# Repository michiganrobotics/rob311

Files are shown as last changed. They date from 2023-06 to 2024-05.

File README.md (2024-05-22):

# Robotics 311: How to Build Robots and Make Them Move

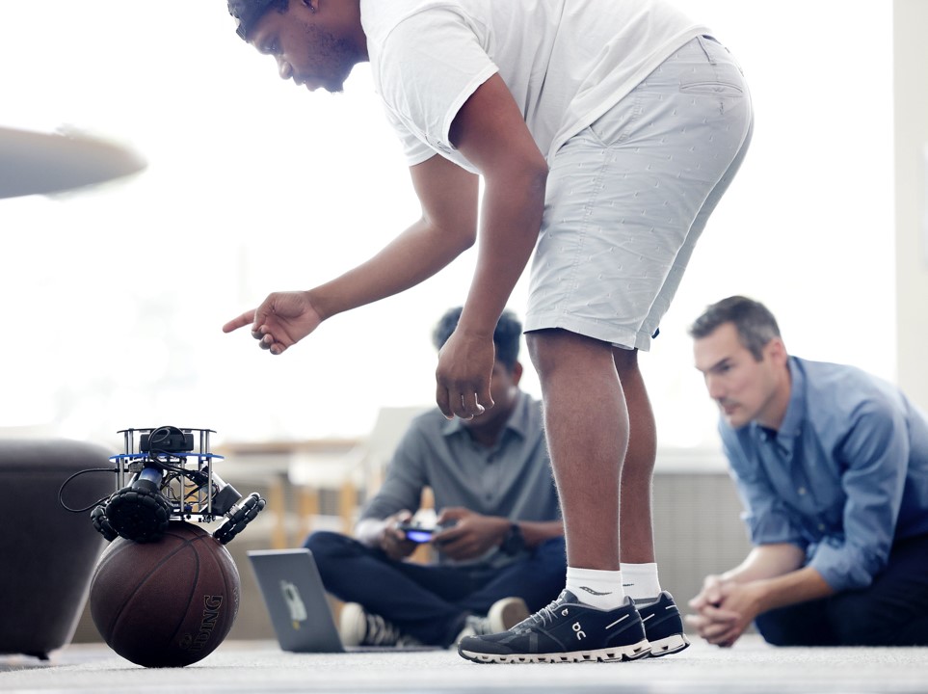
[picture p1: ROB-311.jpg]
Yves points at a ballbot


ROB 311 is an undergraduate robotics course at the University of Michigan that introduces the fundamentals of mechanical design, control, fabrication, actuation, instrumentation, and computer interfaces required to realize robotic systems. Students will learn to analyze/simulate rigid body kinematics, kinetics, and dynamics, as well as assess the impedance properties of their designs.

This first iteration was offered in Fall 2022. The course is based around building a ballbot, which balances on a basketball to move around.

## Lectures
All lecture videos are available on YouTube: [ROB 311 Fall 2022 Playlist](https://www.youtube.com/watch?v=aZ-mrETfKmE&list=PLdPQZLMHRjDIWDJDjiBKjFe7ETD_rssB9)

If a lecture features additional files, those are located in [lecture files](https://github.com/michiganrobotics/rob311/tree/main/Lecture%20Files).

## Labs and hardware

[Labs](https://github.com/michiganrobotics/rob311/tree/main/Labs) are based around the design and build of the ballbot, requiring certain hardware and access to machines, including 3D printer, laser cutter, and water jet.

The parts list (or [see full bill of materials](https://github.com/michiganrobotics/rob311/blob/main/Resources/Ballbot%20Bill%20of%20Materials.pdf)):
- Raspberry Pi Pico
- BlinkM led
- 3 Pololu 37D gearmotors
- 3 motor couplers
- acrylic sheets
- velcro strips
- 6 omni wheel halves
- 2 wired mouse
- basketball

Note lab 1, a primer on soldering, is not included in this repository, and lab 5 is skipped.

## Course Plan
| Lecture | Topic | YouTube | Assignments Due |
|---|---|---|---|
| 1 | Introduction to robot development | [Video](https://www.youtube.com/watch?v=aZ-mrETfKmE) | |
| L1 | Lab: Soldering | | |
| 2 | Motors, transmissions, & drivers I  | [Video](https://www.youtube.com/watch?v=Mq1Bgk68PBI) | |
| 3 | Motors, transmissions, & drivers II | [Video](https://www.youtube.com/watch?v=Oz2Eo8m5Dek) | |
| L2 | Lab: Raspberry Pi's | | |
| 4 | Mechanical modeling | [Video](https://www.youtube.com/watch?v=HCKUdEtMk7Y) | |
| 5 | Modeling & design | [Video](https://www.youtube.com/watch?v=dP0wdarfrkY) | HW 1 |
| L3 | Lab: Solidworks | | |
| 6 | Thermal modeling | [Video](https://www.youtube.com/watch?v=CyqpaNBj9x0) | |
| 7 | Manufacturing | [Video](https://www.youtube.com/watch?v=a9g4DT3PtMI) | |
| L4 | Lab: Lasercutting | | |
| 8 | Additive manufacturing | [Video](https://www.youtube.com/watch?v=YzE1I1oQzHI) | |
| 9 | Subtractive manufacturing | [Video](https://www.youtube.com/watch?v=Pls2lRZjnxo) | |
| L6 | Lab: Ballbot assembly | | Ballbot assembled |
| 10 | Manufacturing best practices | [Video](https://www.youtube.com/watch?v=BBs-HmwfgLc) | |
| 11 | Gears, screws & linkages | [Video](https://www.youtube.com/watch?v=xYcbeahHpbk) | |
| L7 | Lab: Python | | |
| 12 | Full planar model | [Video](https://www.youtube.com/watch?v=MVAvgaW5twc) | HW 2 |
| 13 | Torque conversion | [Video](https://www.youtube.com/watch?v=8ChdTWNvGpY) | |
| L8 | Lab: Closed loop control | | |
| 14 | Kinematic conversions | [Video](https://www.youtube.com/watch?v=uLpom1g87a0) | |
| L9 | Lab: Kinematics | | |
| 15 | Sensors | [Video](https://www.youtube.com/watch?v=9VtycgTxyyI) | HW 3 |
| 16 | Digital communications | [Video](https://www.youtube.com/watch?v=Y-86CC3WgMU) | |
| L10 | Lab: Stability control | | |
| 17 | Omni wheels | [Video](https://www.youtube.com/watch?v=Ykprm8sEqzw) | |
| 18 | Ballbot work session | No lecture | |
| L11 | Lab: Outer velocity loop control | | |
| 19 | Review | [Video](https://www.youtube.com/watch?v=hH9S14uijNM) | Midterm (not publicly available) |
| L12 | Lab: Virtual environments | | |
| 20 | Control | [Video](https://www.youtube.com/watch?v=tzFXzcDsMec) | HW 4 |
| 21 | Control loop structure | [Video](https://www.youtube.com/watch?v=KcQr0awXiuQ) | |
| L13 | Lab: Filtering data | | |
| 22 | Ballbot work session | No lecture | |
| 23 | Filtering data | [Video](https://www.youtube.com/watch?v=sBFdfnljp9M) | |
| L14 | Lab: Ballbot work session | | HW 5 |
| 24 | Steering control | [Video](https://www.youtube.com/watch?v=FliyuyiXhro) | |
| 25 | Final competition | | |

## Credits
- Elliott Rouse, Associate Professor, U-M
- Yves Nazon
- Senthur Ayyappan

## For more
- [University of Michigan Robotics](https://robotics.umich.edu)
- [Michigan Robotics Twitter](http://twitter.com/umrobotics)
- [Michigan Robotics Instagram](http://instagram.com/umrobotics/)
- [Michigan Robotics LinkedIn](https://www.linkedin.com/company/university-of-michigan-robotics/)

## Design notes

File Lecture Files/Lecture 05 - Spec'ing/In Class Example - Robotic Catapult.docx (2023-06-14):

In Class Example – Robotic Catapult

J_T : Total Inertia

J_m : Motor Inertia

J_(pm) : Point Mass Inertia= ml_a^2

τ_l : External Load=J_(pm) θ- mgl_a cos(θ)

ϕ_m : Motor Position=Nθ

Current Equation

k_t i=J_T ϕ_m +bϕ_m +(τ_l)/(ηN)

k_t i= (J_m +(ml_a^2)/(ηN^2))Nθ+bNθ+ (mgl_a cos(θ))/(ηN)

k_t i= J_m Nθ+(ml_a^2 θ)/(ηN)+bNθ+ (mgl_a cos(θ))/(ηN)

i=(J_m Nθ+(ml_a^2 θ)/(ηN)+bNθ+ (mgl_a cos(θ))/(ηN))/(k_t)

Voltage Equation

V=iR+L(di)/(dt)+k_t ϕ_m

V=iR+L(di)/(dt)+k_t Nθ

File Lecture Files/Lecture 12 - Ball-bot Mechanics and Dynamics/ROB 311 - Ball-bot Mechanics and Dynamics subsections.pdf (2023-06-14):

Planar System Modeling and Control

## 2 Planar System Modeling and Control

### 2.1 Model

### 2.1.1 Model Description

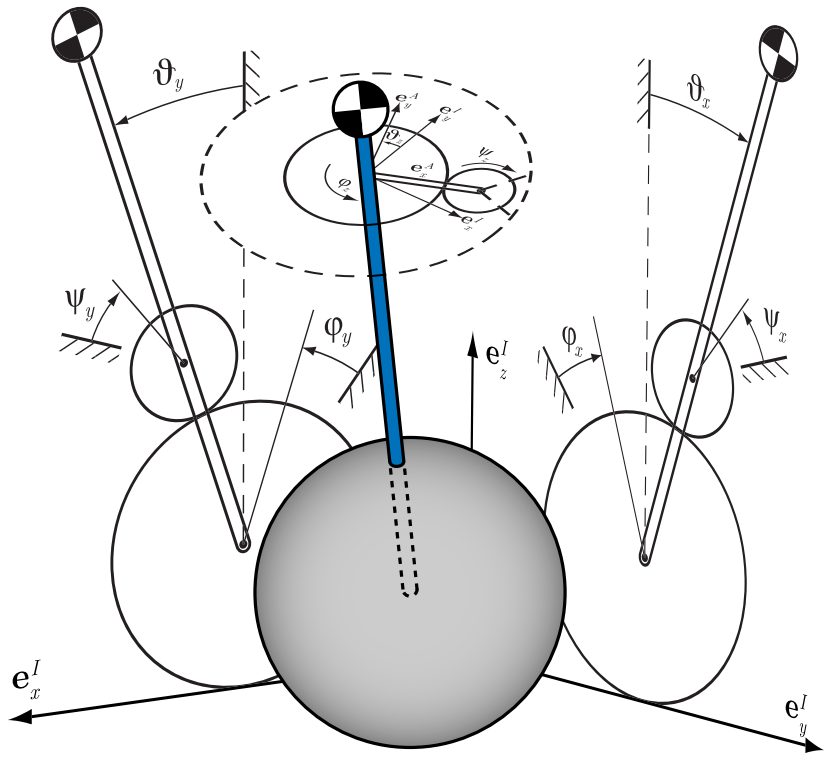
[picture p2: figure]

Figure 2.1: The three planar models, each model consists of the ball, the body and the actuating wheel

The three-dimensional system is divided into three independent planar models (fig: 2.1), where each can be described with the following two Degrees of Freedom (DoF):

- 1 DoF for the rotation/translation of the ball
- 1 DoF for the rotation of the body

The propulsion system, which is composed of three omniwheels, is modeled as one virtual actuating wheel in each plane which drives the ball. That particular wheel does of course not have the same position and speed as the omniwheels in the real system. Therefore, conversions are needed (see section 2.3).

2.1 Model | Planar System Modeling and Control
| The states of the system are the orientation angles and angle rates of the body and the
| position and speed of the ball. Since all these states are measured by the IMU and the
| motor encoders, the system outputs are equal to the states. The inputs are the torques
generated by the motors.

### 2.1.2 Assumptions

| In the planar system modeling, the system is treated as three independent planar models.
| Therefore no coupling effects between these three models are taken into account. Two
| of them (the ones in the xz- and yz-plane) are identical and very similar to an inverted
| pendulum, as shown on the left side of figure 2.2. The third one (in the xy-plane)
| describes the rotation around the z-axis in the body fixed reference frame, often described
| as the rotation around the ballbot’s own axis (right side of figure 2.2).
| The system is assumed to consist of three rigid bodies: the ball, the actuating wheel and
| the body. The three motors and omniwheels are therefore simplified as one actuating
wheel that fits in a plane.
Additionally, the following assumptions are made:
| No slip The contact points between the ball and the ground and between the wheels and
| the ball are assumed to be free of slippage. The system construction is optimized
| in order to minimize possible slipping. Thus, the torques applied have to be limited
| within the range that does not cause slippage in order to ensure the validity of the
model.
| No friction Even though friction occurs in the system, it is neglected except for the
| rotation of the ball on the ground around the z-axis, because this is the friction
| with the biggest impact. Non-continuous friction is hard to represent analytically
| and would generate equations much more complex than without friction. Also, the
precise measuring of friction is difficult.
| No deformation Because of its synthetic coating, deformation appears at the contact
| points of the ball. This has to be neglected in order to keep complexity at a
manageable level.
| Fast motor dynamics The power electronics control the dynamics of the motors much
| faster than the controller the dynamics of the stabilized system. Consequently, the
| motor torques are modeled to be the inputs of the system.
| Ball moves only horizontally In order to keep the prerequisite for the no slip condition,
| vertical movement of the ball has to be neglected. Finally, this model is designed
| to move primarily on flat surfaces without steep inclination.

Planar System Modeling and Control | 2.1 Model

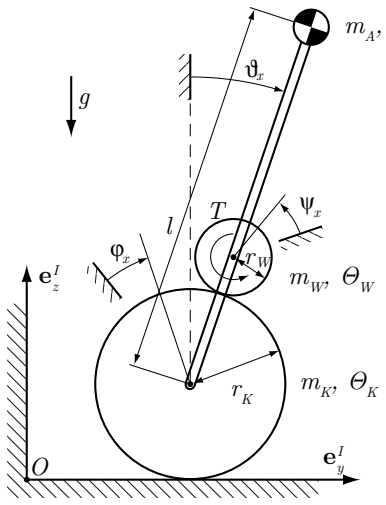
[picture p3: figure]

## mA, ΘA

### rK sinα

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
ΘW,xy

ΘA,xy

Figure 2.2: Sketch of the planar models showing the coordinates and parameters. On the left side the model for the two vertical planes and on the right side the xy-plane model is shown.

### 2.1.3 Coordinates

To describe the system, the coordinates shown in figure 2.2 are used. ϑx,y,z represent the orientation of the body, ϕx,y,z represent the orientation of the ball and ψx,y,z are the angles of the virtual actuating wheels. Using the following minimal coordinates, the system can be completely described.

~qxy =

"
ϕz
ϑz
~qyz =

"
ϕx
ϑx
~qxz =

"
ϕy
ϑy
(2.1)

### 2.1.4 Binding Equations

All coordinates can be expressed as functions of the minimal coordinates, which is necessary in order to derive the equations of motion. The positions of the ball, the wheel and the body can be written as follows, using the rolling constraint¹
xK = ϕxrK | (2.2)
xW = ϕxrK + sin ϑx · (rK + rW ) | (2.3)
xA = ϕxrK + sin ϑx · l | (2.4)

Analogous relations are valid for the y coordinates.

1Meaning, that for example the balls position is determined by its slip free rolling on the ground.

2.1 Model | Planar System Modeling and Control

The rotation of the actuating wheel expressed as a function of the minimal coordinates yields the following equations.

ψ˙
x =

rK
rW
ϕ˙x − ϑ˙
x
− ϑ˙
x | (2.5)

ψ˙
y =

rK
rW
ϕ˙ y − ϑ˙
y
− ϑ˙
y | (2.6)

ψ˙
z =

rK
rW
- sin α · ( ˙ϕz − ϑ˙
z) (2.7)

The derivation can be found in the appendix B.1.

### 2.1.5 Forces

In order to get an idea of the forces taking effect in the system, a Newton/Euler approach

is used to derive analytical equation for the forces shown in figure 2.3. The detailed equations are listed in the appendix B.3.

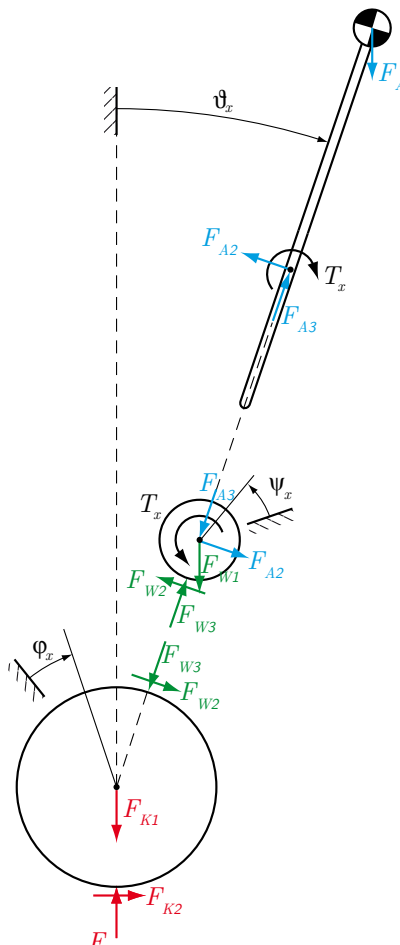
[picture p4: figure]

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
Figure 2.3: Free-body diagrams for the three parts of the model, showing all internal forces

Planar System Modeling and Control | 2.2 Dynamics

### 2.1.6 Parameters

In table 2.1, the parameters describing the system are listed. Numeric values are derived by measuring or from the CAD model. Calculations of the moments of inertia are

presented in section 2.3.2.

Description | Variable | Value
Mass of the ball Mass of the virtual actuating wheel Mass of the body Radius of the ball Radius of the omniwheels Radius of the body (cylinder) Height of the center of gravity Inertia of the ball Inertia of the actuating wheel in the yz-/xz-plane Inertia of the actuating wheel in the xy-plane Inertia of the body Inertia of the body in the xy-plane Gravitational acceleration Gear ratio | mK mW mA rK rW rA l ΘK ΘW ΘW,xy ΘA ΘA,xy g iGear | 2.29 kg 3 kg 9.2 kg 0.125 m 0.06 m 0.1 m 0.339 m 0.0239 kgm² 0.00236 kgm² 0.00945 kgm² 4.76 kgm² 0.092 kgm² 9.81 m/s² 26

Table 2.1: Parameters of the planar system

### 2.2 Dynamics

### 2.2.1 Approach

For the derivation of the equations of motion, the Lagrangian method was selected as the common approach for that kind of problems. The following steps are needed:

- express kinetic (T) and potential (V) energy of all rigid bodies as a function of the

minimal coordinates,

- write non-potential forces as a function of the minimal coordinates,
- solve the Lagrange equation for the second derivative of the minimal coordinates.

The calculations are made for the yz-plane model, which is identical to the xz-plane model, and for the xy-plane model as well.

Planar System Modeling and Control | 2.3 Conversions to the Real System

Since a controller for the planar model is going to be implemented on the real system,

conversions have to be calculated. In order to be able to control the real system, the
torques on the virtual motors have to be converted into the torques for the real motors.

Definitions

One element of the real system (omniwheel driven by a motor) is shown on the left side

in figure 2.4. It actuates the ball by scrolling on a circle on the ball, characterized by the motor arrangement angle α.
The right side of figure 2.4 shows a top view on the real actuating system where the torque of each omniwheel generates a tangential force on the surface of the ball.

## cosα

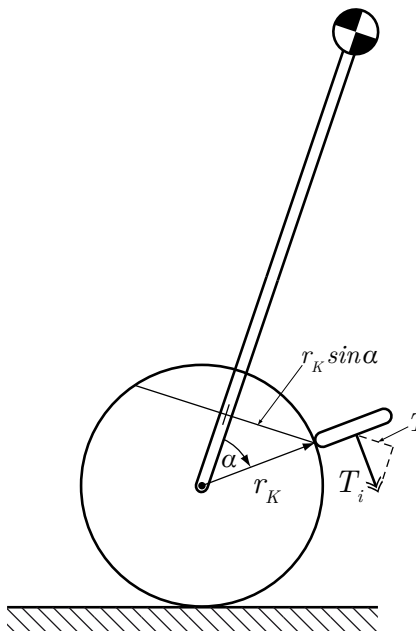
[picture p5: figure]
sinα

Ti

## rK sinα

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
Figure 2.4: On the left side the arrangement of one real omniwheel is shown. The sketch on the right side shows the torques and tangential forces generated by the real actuating system, the dashed arrows mark the virtual torques.

FW,1, FW,2, FW,3 in figure 2.4 denote the tangential forces on the ball generated by torques of the motors in the real configuration, consequently these are functions of T1,2,3. The levers for this configuration are denoted as rKW,1, rKW,3, rKW,3. For the virtual configuration, the notation FW,x, FW,y, FW,z is used for the tangential forces (as functions of Tx,y,z) and rKW,x, rKW,y, rKW,z for the levers. All those are geometrical

relationships one can read out of figure 2.4. In the appendix C.1 the relationships are written out in full.

2.3 Conversions to the Real System | Planar System Modeling and Control

Torque on the ball

Once the relationships are given, the torque on the ball from the real and the virtual driving mechanism can be calculated. The torque is equal to the product of force and lever. Hence the torques for the real and the virtual configuration are calculated as follows.

TKW,i = rKW,i × FW,i | for i = 1, 2, 3 | (2.28)
TKW,j = rKW,j × FW,j | for j = x, y, z | (2.29)

Solution

Of course, the overall torque needs to be conserved:

TKW,1 + TKW,2 + TKW,3 = TKW,x + TKW,y + TKW,z | (2.30)

Solving the relations for the real torques yields:

T1 =

1
3

·

Tz +

2
cos α
- (Tx · cos β − Ty · sin β)
(2.31)

T2 =

1
3

·

Tz +

1
cos α

·

sin β · (−

√
3Tx + Ty) − cos β · (Tx +

√
3Ty)
(2.32)

T3 =

1
3

·

Tz +

1
cos α

·

sin β · (

√
3Tx + Ty) + cos β · (−Tx +

√
3Ty)
(2.33)

Since the system of equation is linear in Tx,y,z, it is straightforward to solve for them as well (see appendix appendix C).

### 2.3.2 Inertia Calculations

The aim of this section is to find a suitable approximation for the moments of inertia of the modeled drive mechanism, which is not the same as in reality. The following approach is made by comparing the energies stored in the real omniwheels and the virtual actuating wheel respectively when driving at a constant velocity.

Approximations for sphere and body

The inertia of the ball is approximated by a hollow sphere, which is a good approximation:

ΘK =

2
3
- mK · r

2
K

The moment of inertia of the body was initially approximated by that of a cylinder. Later, it was directly calculated in the CAD model.

Planar System Modeling

## B Planar System Modeling

B.1 Model for the yz-/xz-Plane

Binding Equations

One planar system has two degrees of freedom. Therefore, it is possible to write any coordinates as a function of the two minimal coordinates ϕx und ϑx.
The following equations are valid for the ball:

xK = ϕxrK

zK = 0

For the actuating wheel:

xW = xK + sin ϑx · (rK + rW )

= ϕxrK + sin ϑx · (rK + rW )

zW = cos ϑx · (rK + rW )

And for the body:

xA = xK + sin ϑx · l

= ϕxrK + sin ϑx · l

zA = cos ϑx · l

The binding equation for ψx is derived by equating the velocities (Starrk¨orper-Geschwindigkeits-Formel) in the contact point between ball and actuating wheel.

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
Planar System Modeling | B.1 Model for the yz-/xz-Plane

Figure B.1: Sketch of the planar model with coordinates and contact points

vA = 0

vB =

x˙ K
0
0

- +

0
ϕ˙x
0

×

rK sin ϑx
0
rK cos ϑx

- =

x˙ K + ˙ϕxrK cos ϑx
0
−rKϕ˙x sin ϑx

vC =

x˙ K
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
(rK + rW ) sin ϑx

0
(rK + rW ) cos ϑx

- +

0
−ψ˙
x
0

×

−rW sin ϑx

0
−rW cos ϑx

=

x˙ K + ϑ˙
x(rK + rW ) cos ϑx + rW ψ˙ x cos ϑx
0
−ϑ˙

x(rK + rW ) sin ϑx − rW ψ˙ x sin ϑx

To comply the no slip condition, the equation vB = vC has to be true. It is then possible to equate the first and third term of vB and vC. Solving these equations by ψ˙
x yields:

ψ˙
x =

rK
rW

( ˙ϕx − ϑ˙

x) − ϑ˙
x | (B.1)

Approach

For the derivation of the equations of motion the Lagrangian method was selected as the common approach for that kind of problems. The following steps are needed:

- express kinetic (T) and potential (V) energy of all rigid bodies as a function of the

minimal coordinates,

- write non-potential forces as a function of the minimal coordinates,
- solve the Lagrange equation for the second derivative of the minimal coordinates.

The calculations are made for the yz-plane model, which is identical to the xz-plane model, and for the xy-plane model as well.

Energies

Ball:

TK =

1
2

mK(rKϕ˙x)

2 +

1
2

ΘKϕ˙

2
x

VK = 0

B.2 Model for the xy-Plane | Planar System Modeling

B.2 Model for the xy-Plane

For the xy-plane model, the same approach is used. The complete derivation is given as follows.

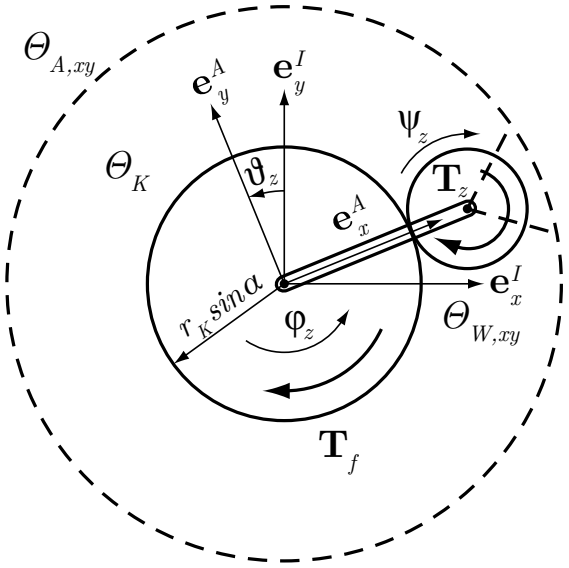
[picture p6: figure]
rK sinα

Figure B.2: Planar model for the xy-plane

Minimal coordinates

The same minimal coordinates are used (see figure B.2).

~q =

"
ϕz
ϑz

Energies

Ball:

TK =

1
2

ΘKϕ˙

2
z

Actuating wheel (Note: ΘW,xy contains the inertias of motors and wheels around ψz).

TW =

1
2

ΘW,xyψ˙²
z

Body (Note: ΘA,xy contains the inertias of motors and wheels around ϑz).

TA =

1
2

ΘA,xyϑ˙²
z

Planar System Modeling | B.2 Model for the xy-Plane

Binding equation

ψ˙
z =

rK
rW
- sin α · ( ˙ϕz − ϑ˙
z) (B.4)

Non-potential forces

From the actuators:

T1 = Tz

J1 =

"
rK
rW
- sin α
−

rK
rW
- sin α

Counter torque:

T2 = −Tz

J2 =

"
0
1

Friction between ball and ground:

T3 = −Tf

J3 =

"
1
0

fNP :

fNP = J1 · T1 + J2 · T2 + J3 · T3 =

"
−Tf +

rK
rW
- sin α · Tz
−

rK
rW
- sin α · Tz + Tz
(B.5)

Equation of motion

Total kinetic energy:

T = TK + TW + TA

Total potential energy:

V = 0

Solving the Lagrange equation for ϕ¨ and ϑ¨ yields:

ϕ¨ = −

(r

2
W ΘA,xy + r

2

KΘW,xy sin² α) · Tf + rKrW ΘA,xy sin α · Tz

r

2
W ΘA,xyΘK + r

2

K(ΘA,xy + ΘK)ΘW,xy sin² α

(B.6)

Conversions

## C Conversions

C.1 Torque Conversion

The planar model uses a virtual wheel to actuate the system. The real system has an actuating structure which differs strongly from the one assumed in the planar model. Since a controller for the planar model is going to be implemented on the real system,

conversions have to be calculated. In order to be able to control the real system, the torques on the virtual motors have to be converted into the torques for the real motors.

Definitions

One element of the real system (omniwheel driven by a motor) is shown on the left side

in figure C.1. It actuates the ball by scrolling on a circle on the ball, characterized by the

motor arrangement angle α.
The right side of figure C.1 shows a top view on the real actuating system where the torque of each omniwheel generates a tangential force on the surface of the ball.

## cosα

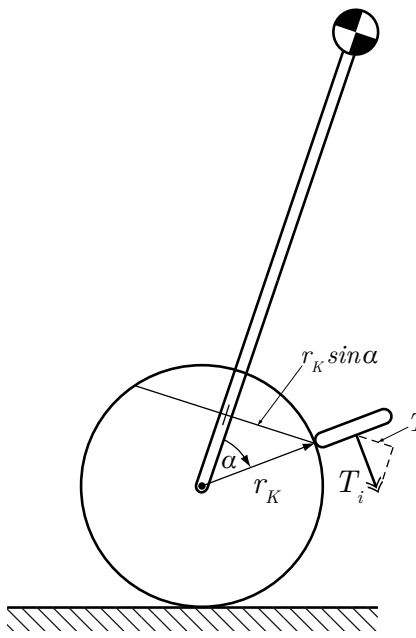
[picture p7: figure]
sinα

Ti

## rK sinα

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
Figure C.1: Torques and tangential forces generated by the real actuating system

The following relationships are read out of figure C.1.

C.1 Torque Conversion | Conversions

Tangential forces of the real configuration:

FW,1 =

T1
rW

·

− sin β

cos β
0

- (C.1)

FW,2 =

T2
rW

·

− sin(β +

2/3 π)
cos(β +

2/3 π)

0

- (C.2)

FW,3 =

T3
rW

·

− sin(β −

2/3 π)
cos(β −
2/3 π)

0

- (C.3)

Lever for real configuration:

rKW,1 = rK ·

cos β sin α
sin β sin α
cos(α

- (C.4)

rKW,2 = rK ·

cos(β +

2/3 π) sin(α)
sin(β +

2/3 π) sin(α)
cos(α)

- (C.5)

rKW,3 = rK ·

cos(β −

2/3 π) sin(α)
sin(β −

2/3 π) sin(α)
cos(α)

- (C.6)

Tangetial forces of the virtual configuration plane:

FW,x =

Tx
rW

·

0
1
0

- | (actually y-direction) | (C.7)

FW,y =

Ty
rW

·

1
0
0

- | (actually x-direction) | (C.8)

FW,z =

Tz
rW

·

− sin β

cos β
0

- (C.9)

Conversions | C.1 Torque Conversion

Lever for the virtual configuration plane:

rKW,x = rKW,y = rK ·

0
0
1

- (C.10)

rKW,z = rK ·

cos β · sin α
sin β · sin α

0

- (C.11)

Torque on the ball

With given relationships the torque on the ball from the real and the virtual driving mechanism can be calculated.
Torques on the Ball from the real omniwheels:
TKW,1 = rKW,1 × FW,1 | (C.12)
TKW,2 = rKW,2 × FW,2 | (C.13)
TKW,3 = rKW,3 × FW,3 | (C.14)

Torques on the Ball from the virtual omniwheels:

TKW,x = rKW,x × FW,x | (C.15)
TKW,y = rKW,y × FW,y | (C.16)
TKW,z = rKW,z × FW,z | (C.17)

Solution

Following equation describes that the two different systems need to introduce the same torque on the ball.

TKW,1 + TKW,2 + TKW,3 = TKW,x + TKW,y + TKW,z | (C.18)

The relationship between real and virtual driving mechanism can be obtained by solving for the unknowns.

C.2 Inertia Calculations | Conversions

Solved for real motor torques:

T1 =

1
3

·

Tz +

2
cos α
- (Tx · cos β − Ty · sin β)
| (C.19)

T2 =

1
3

·

Tz +

1
cos α

·

sin β · (−

√
3Tx + Ty) − cos β · (Tx +

√
3Ty)
| (C.20)

T3 =

1
3

·

Tz +

1
cos α

·

sin β · (

√
3Tx + Ty) + cos β · (−Tx +

√
3Ty)
| (C.21)
| (C.22)

Solved for virtual motor torques:

Tx =cos α ·

T1 · cos β − T2 · sin(β +

π
6

) + T3 · sin(β −

π
6

)

| (C.23)

Ty =cos α ·

−T1 · sin β − T2 · cos(β +

π
6

) + T3 · cos(β −

π
6

)

| (C.24)
Tz =T1 + T2 + T3 | (C.25)

C.2 Inertia Calculations

The aim of this section is to find a suitable approximation for the moments of inertia of the modeled drive mechanism, which is not the same as in reality. The following approach is made by comparing the energies stored in the real omniwheels and the virtual actuating wheel respectively, when driving at a constant velocity.

Approximations for ball and body

ΘK =

2
3

mKr

2
K | (hollow sphere) | (C.26)

ΘA =

1
4
- mA · r

2
A +

1
2
- mA · h

2 + mA · l

2
| (cylinder) | (C.27)

Motors and omniwheels

The real rotor inertia of a motor is given by

ΘM = 3.33 · 10⁻⁶
kgm²

and the real inertia of an omniwheel is calculated as:

ΘOW =

1
2

mOW r

2

W = 900 · 10⁻⁶
kgm²

Since the reduction of the gear box is i = 26, the rotor of the motor turns 26 times faster. Therefore, a factor i

2
is added to calculate the energy (E = 1/2 · Θ · v

2
). So

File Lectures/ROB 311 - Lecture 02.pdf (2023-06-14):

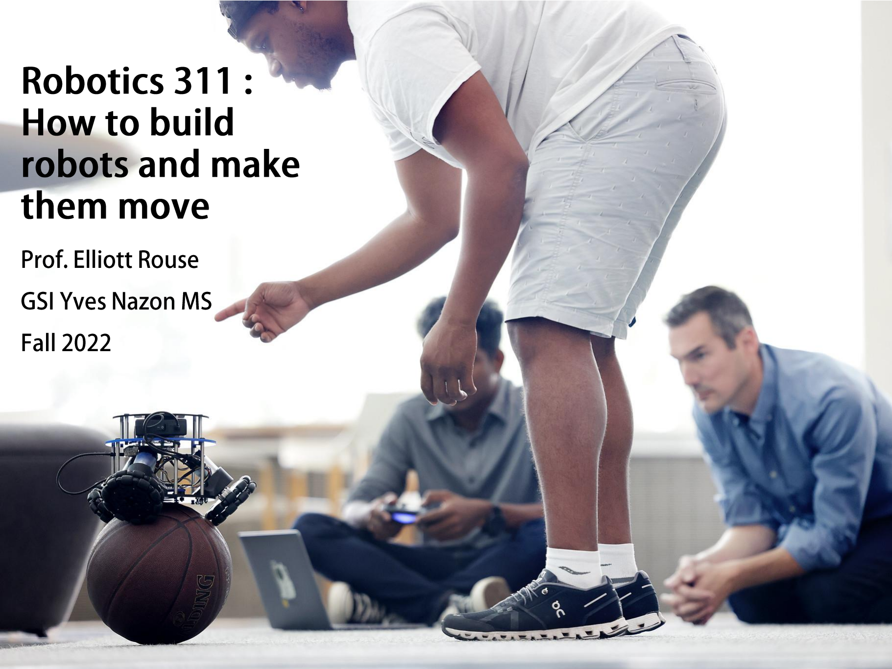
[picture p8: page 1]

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
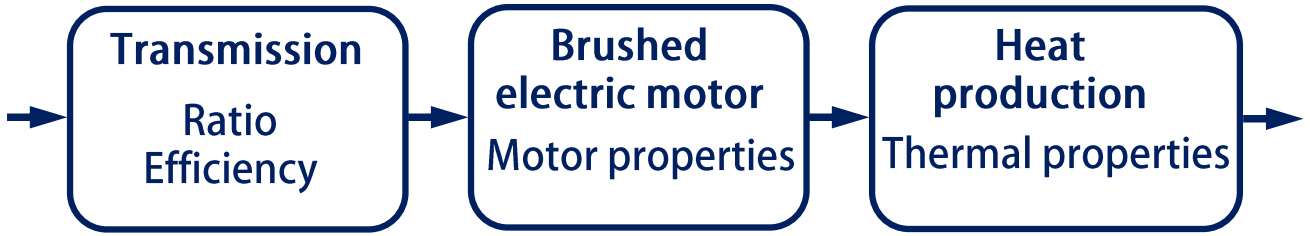
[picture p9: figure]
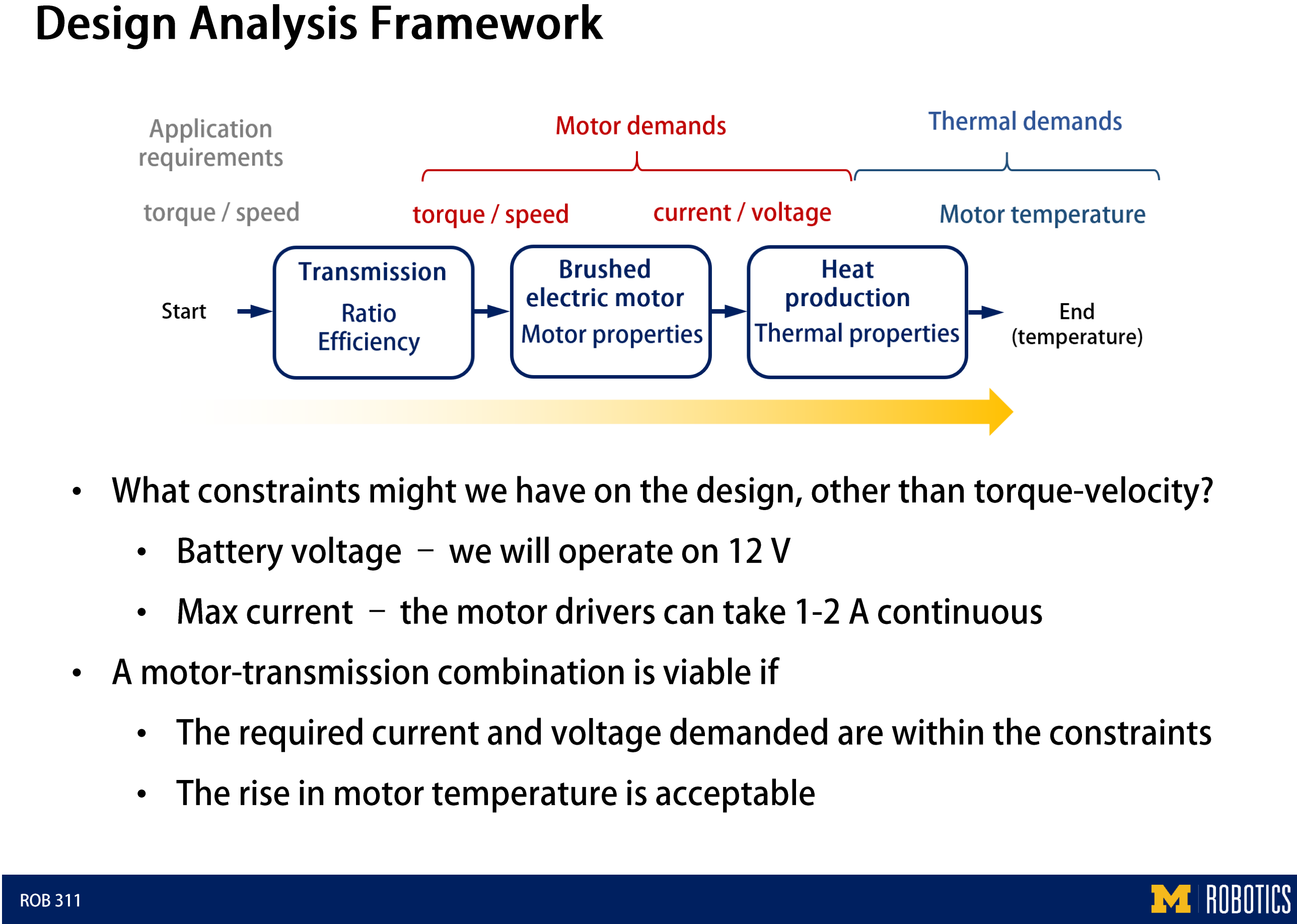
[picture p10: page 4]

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
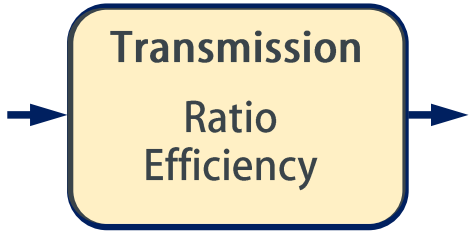
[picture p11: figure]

Ratio = N

Velocity = ψሶ
Torque = Tw

Velocity = ψሶ ∙ N
Torque =Tw
N

•

•

•

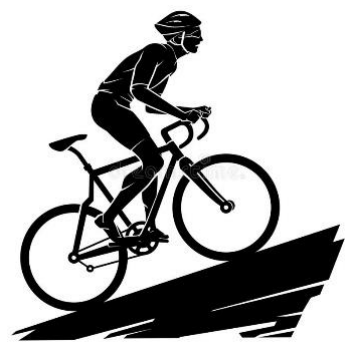
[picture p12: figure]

•

•

•

•

•

•

Ratio = N

Velocity = ψሶ
Torque = Tw

Velocity = ψሶ ∙ N
Torque =Tw
N

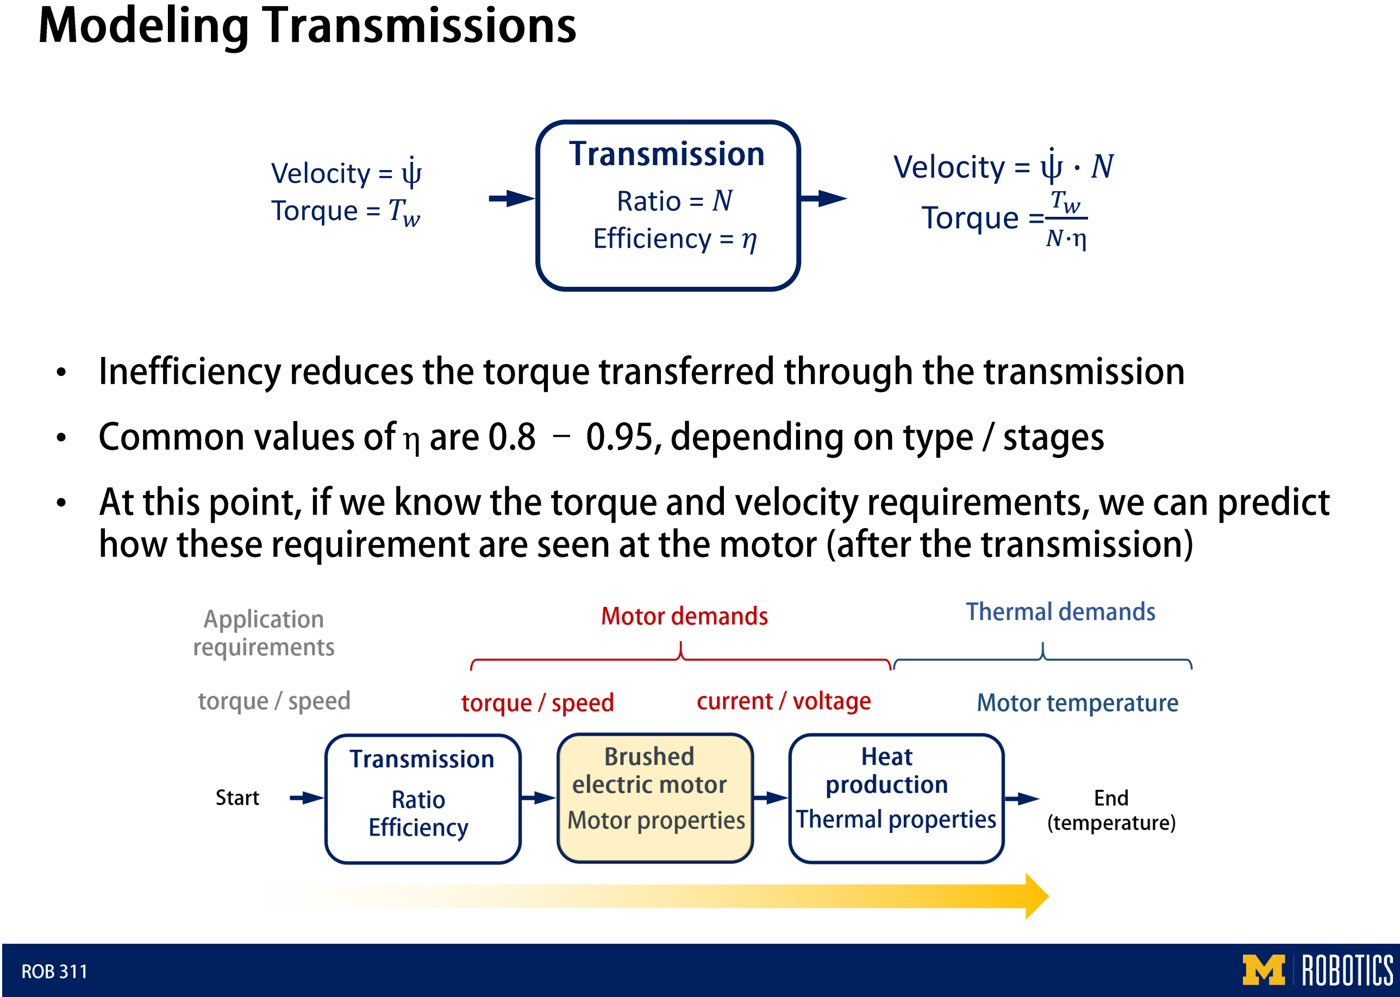
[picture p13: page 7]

•

- η

•

Ratio = N
Efficiency = η

Velocity = ψሶ
Torque = Tw

Velocity = ψሶ ∙ N
Torque = Tw
N∙η

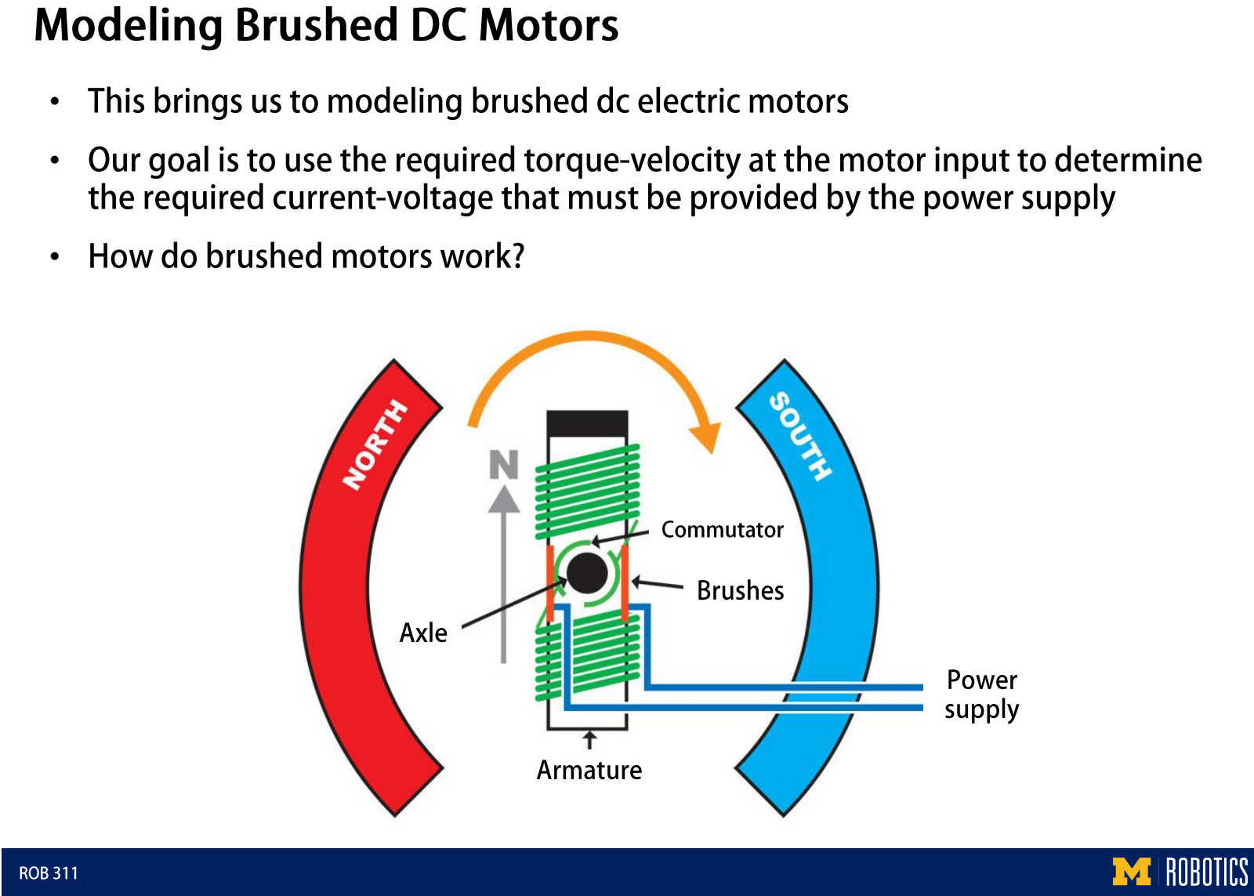
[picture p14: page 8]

•••

•

•••

•••

→

•

••••

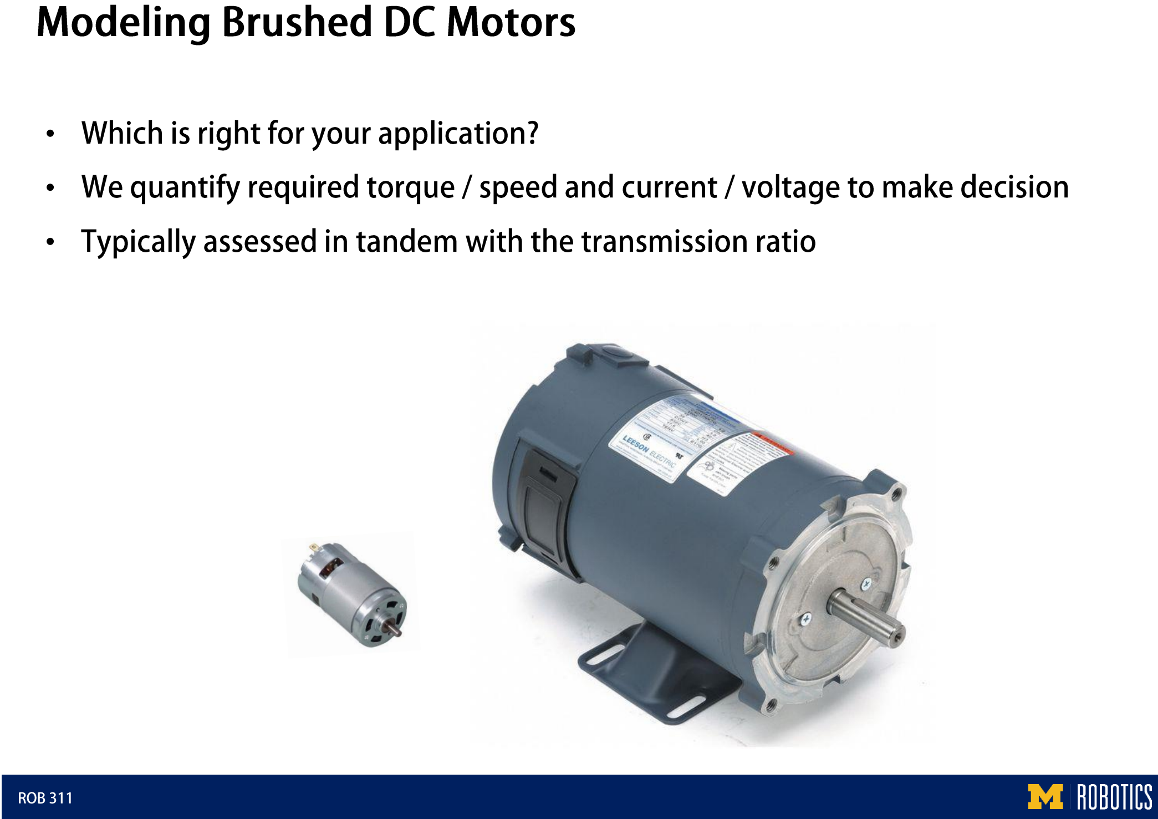
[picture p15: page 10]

•••

•

•

•

•

•

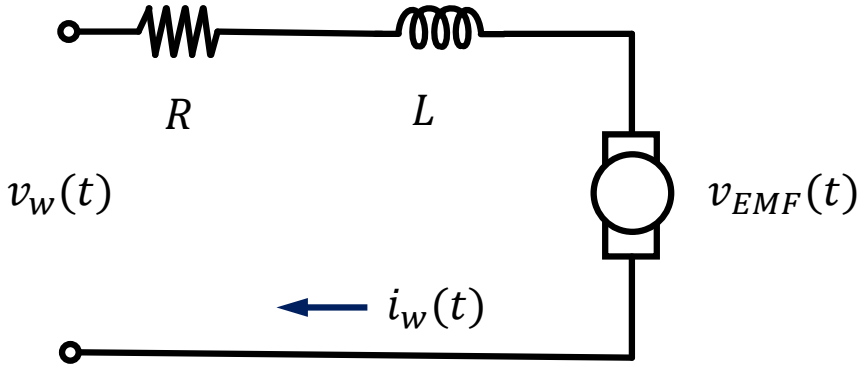
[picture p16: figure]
vEMF(t)
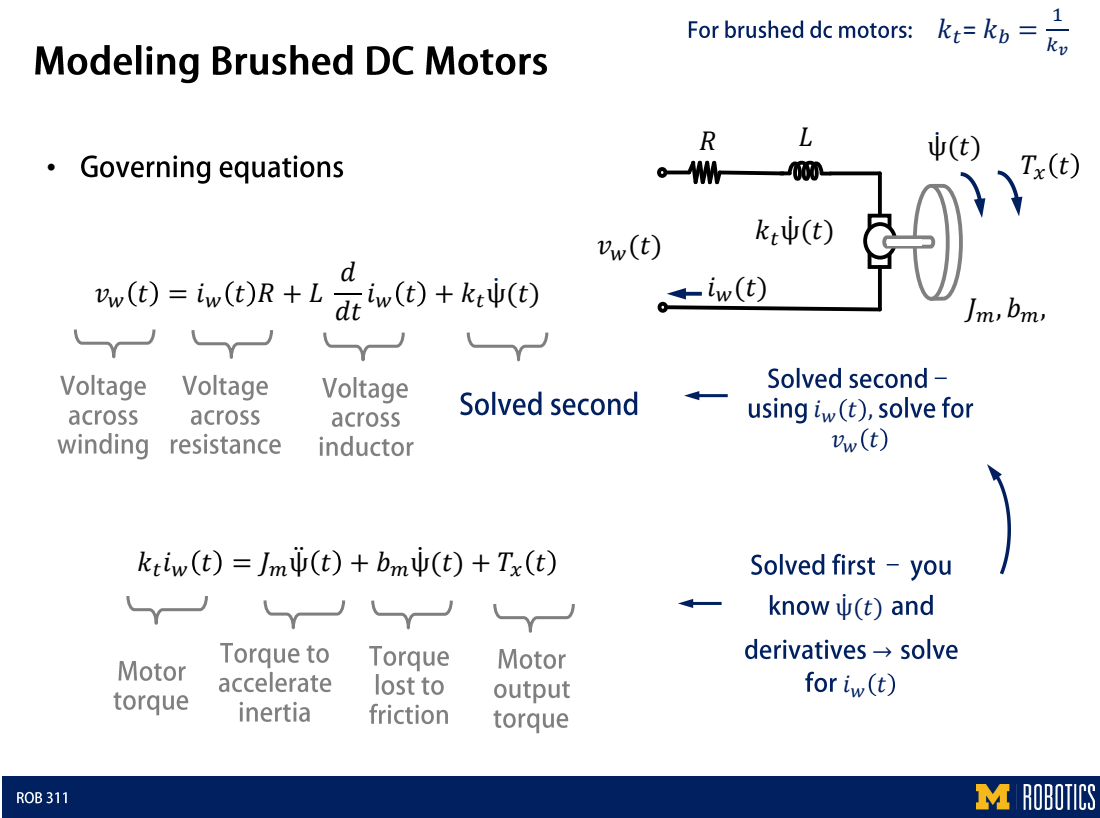
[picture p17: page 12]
d dtiw t + ktψሶ (t); ktψሶ (t)

iw t = Jmψሷ t + bmψሶ (t) + Tx t

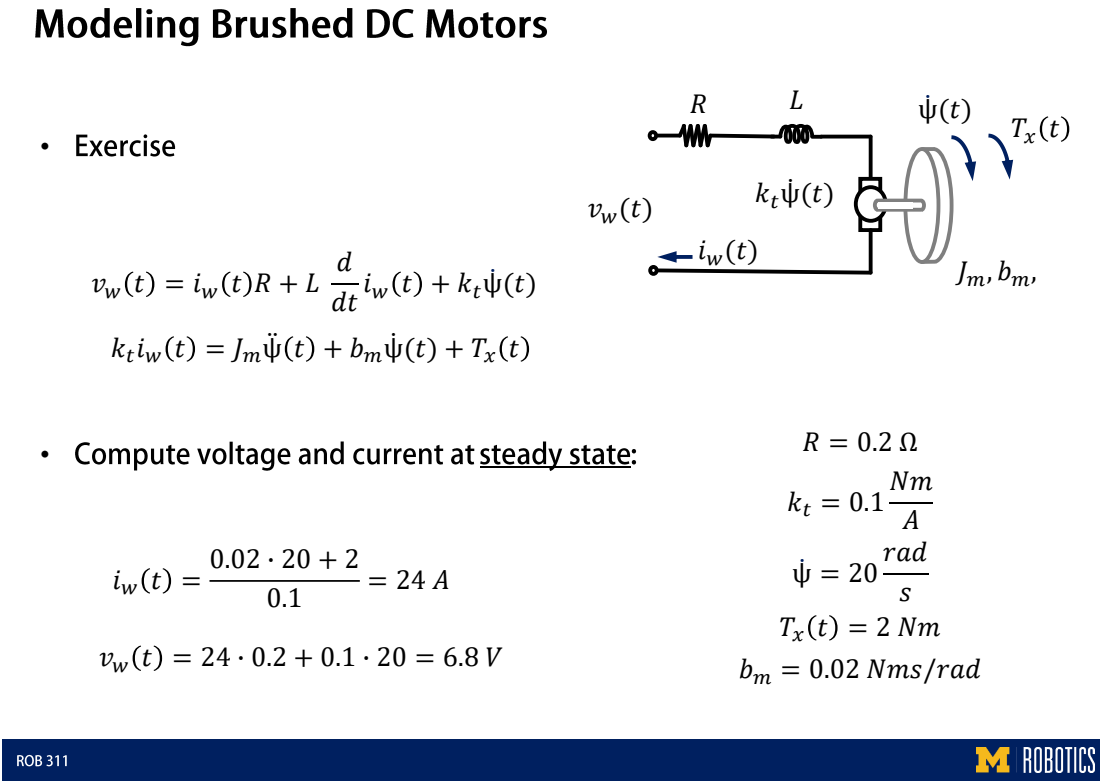
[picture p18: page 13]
d dtiw t + ktψሶ (t); ktψሶ (t); rad s

iw t = Jmψሷ t + bmψሶ (t) + Tx t

bm = 0.02 Nms/rad

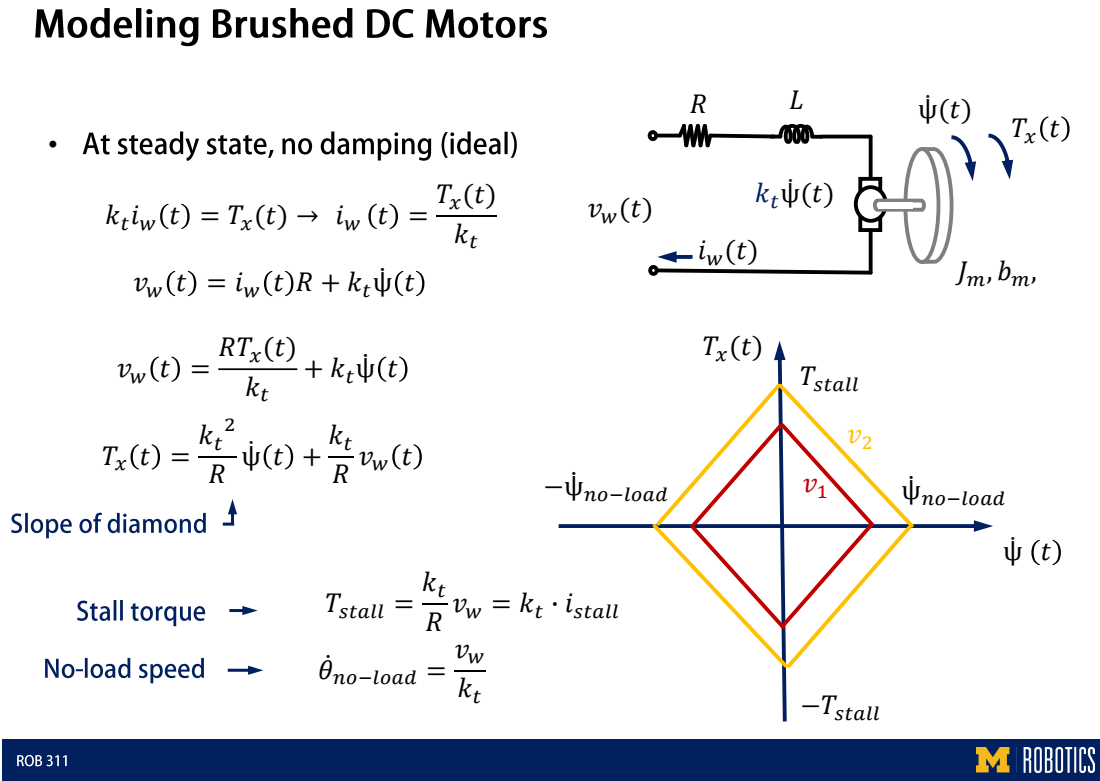
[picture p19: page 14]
ktψሶ (t); RTx(t) kt; + ktψሶ t; Tstall =; ∙ istall; θሶ no−load =; Tstall; −Tstall; no−load ψሶ; no−load

vw t = iw t R + ktψሶ t

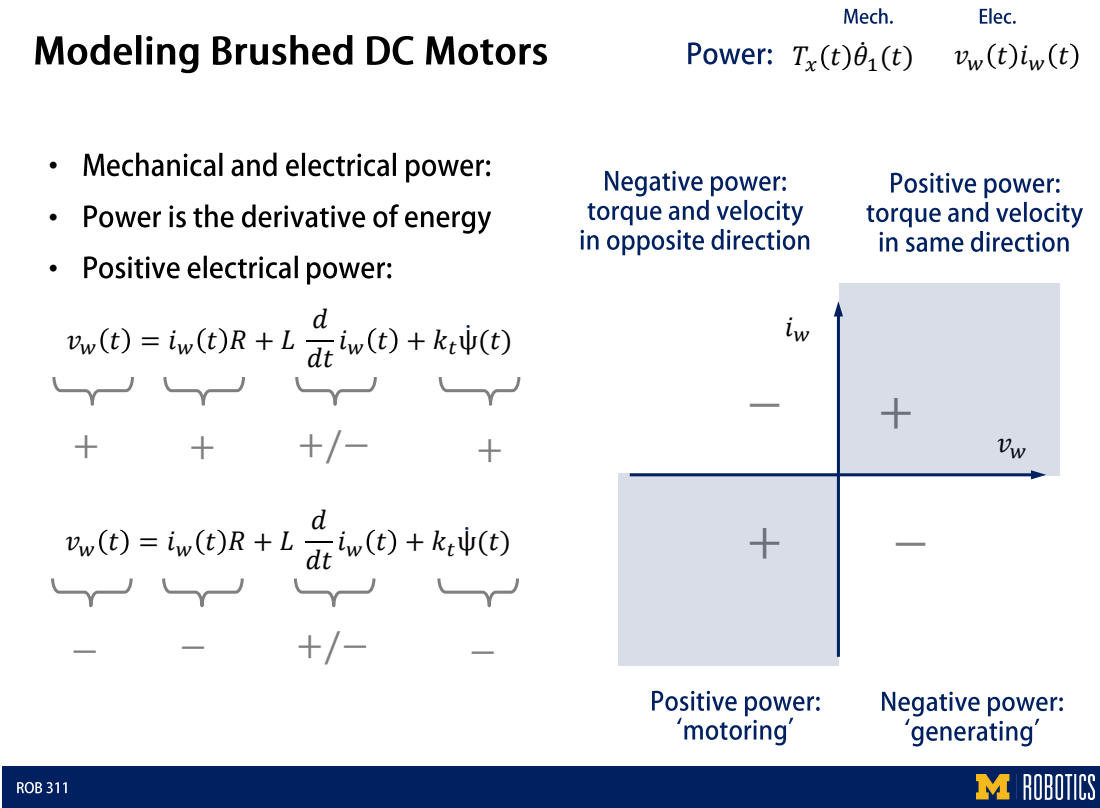
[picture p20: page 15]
d dtiw t + ktψሶ (t)

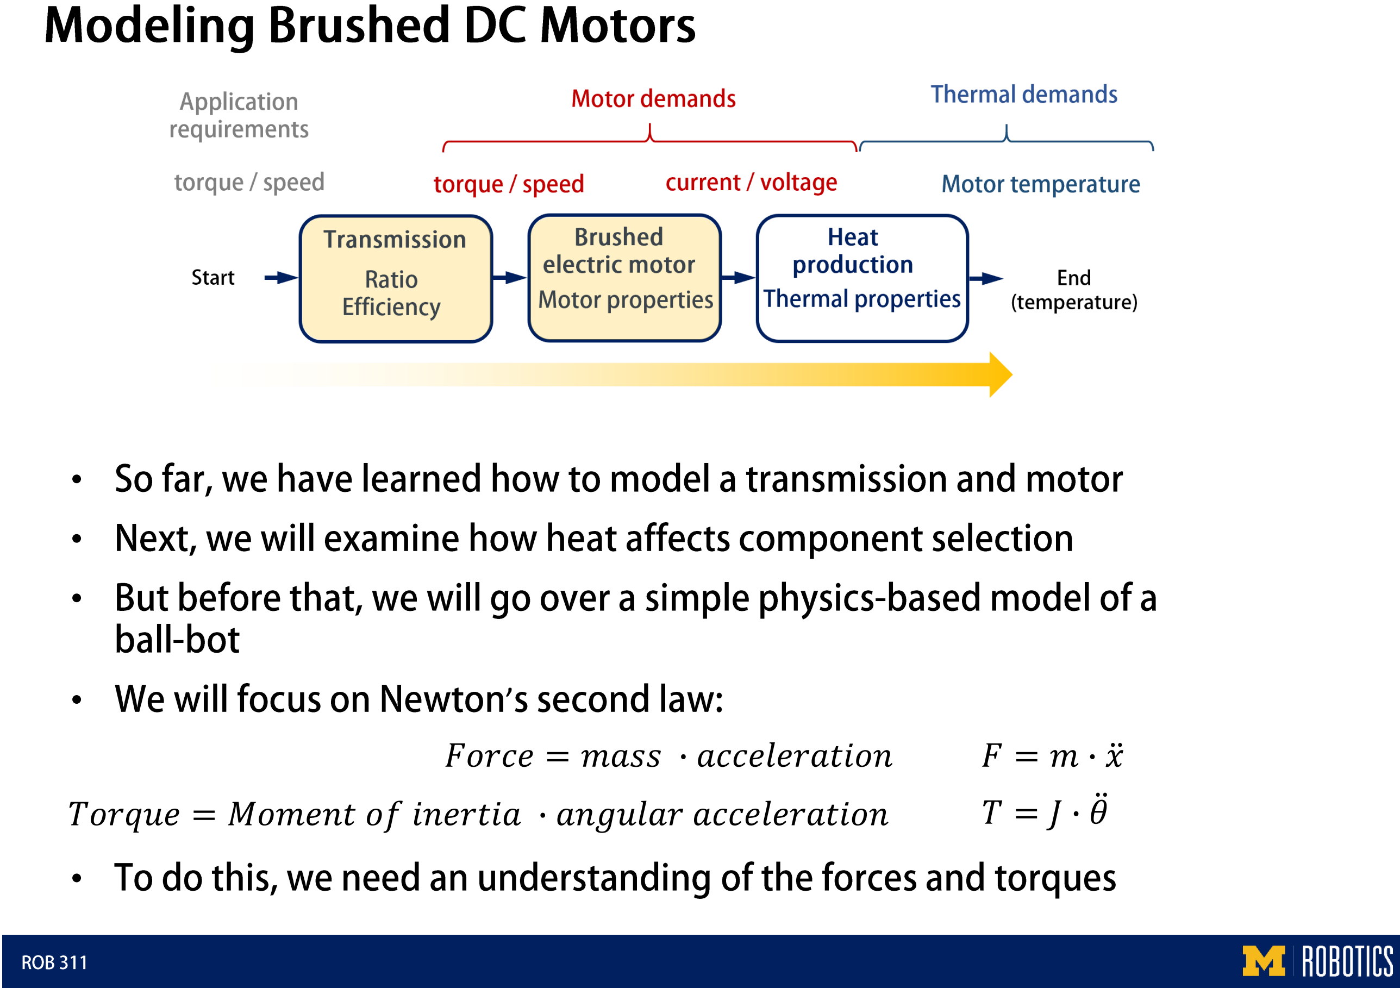
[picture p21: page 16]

•

•

•

- ’

•

Force = mass ∙ acceleration | F = m ∙ xሷ
Torque = Moment of inertia ∙ angular acceleration | T = J ∙ θሷ

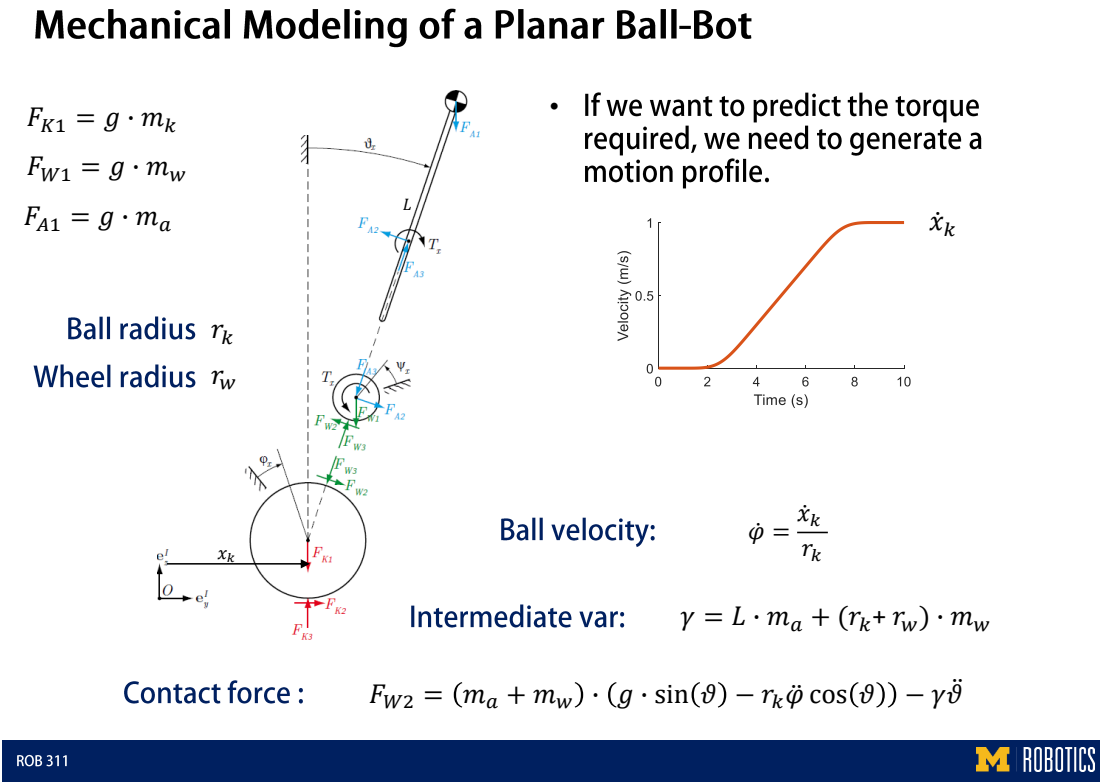
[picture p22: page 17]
xሶk; xሶk rk

FW2 = ma + mw ∙ g ∙ sin θ − rkφሷcos θ − γθሷ

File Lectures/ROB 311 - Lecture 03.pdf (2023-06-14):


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
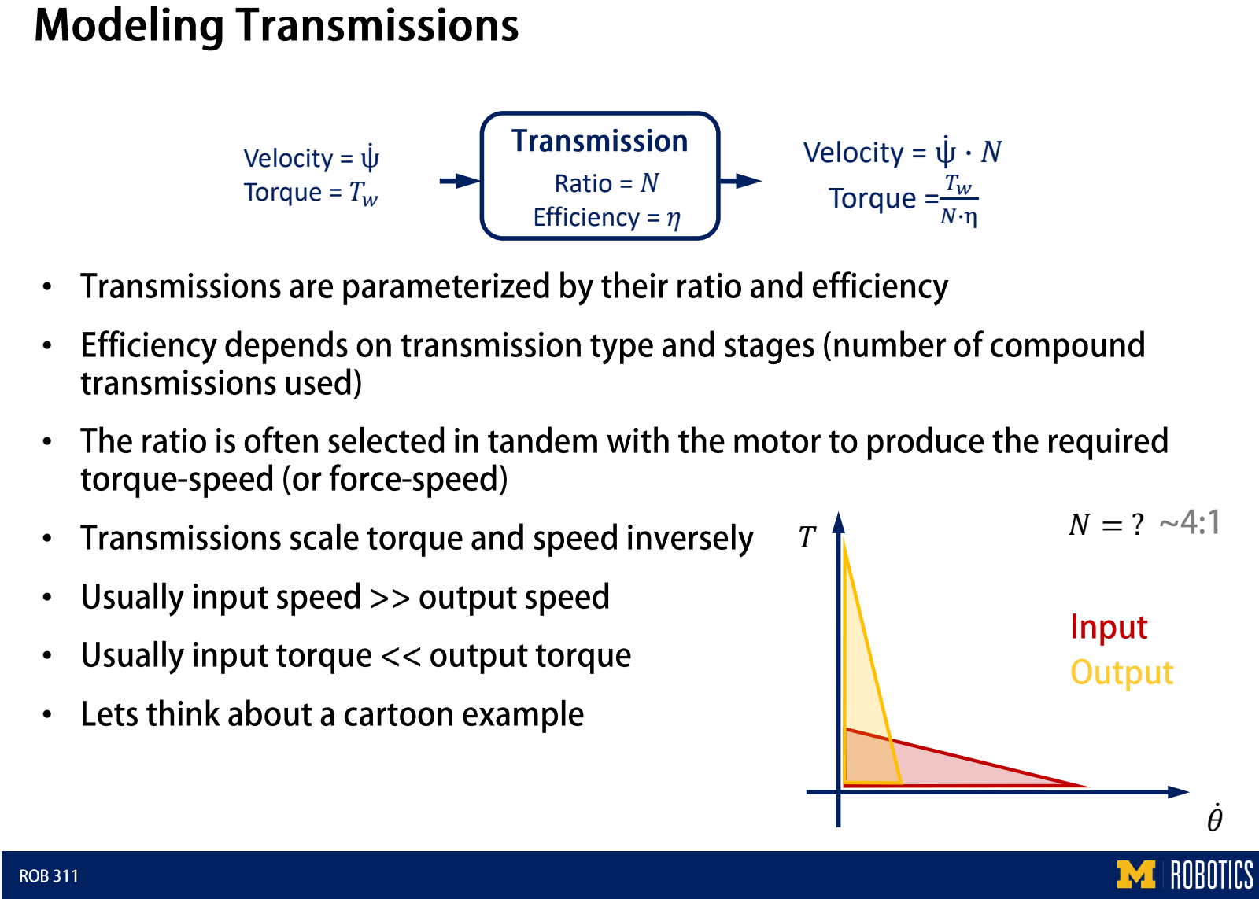
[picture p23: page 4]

•

•

•

•

•

•

•

Ratio = N
Efficiency = η

Velocity = ψሶ
Torque = Tw

Velocity = ψሶ ∙ N
Torque = Tw
N∙η

T

θሶ

N = ?

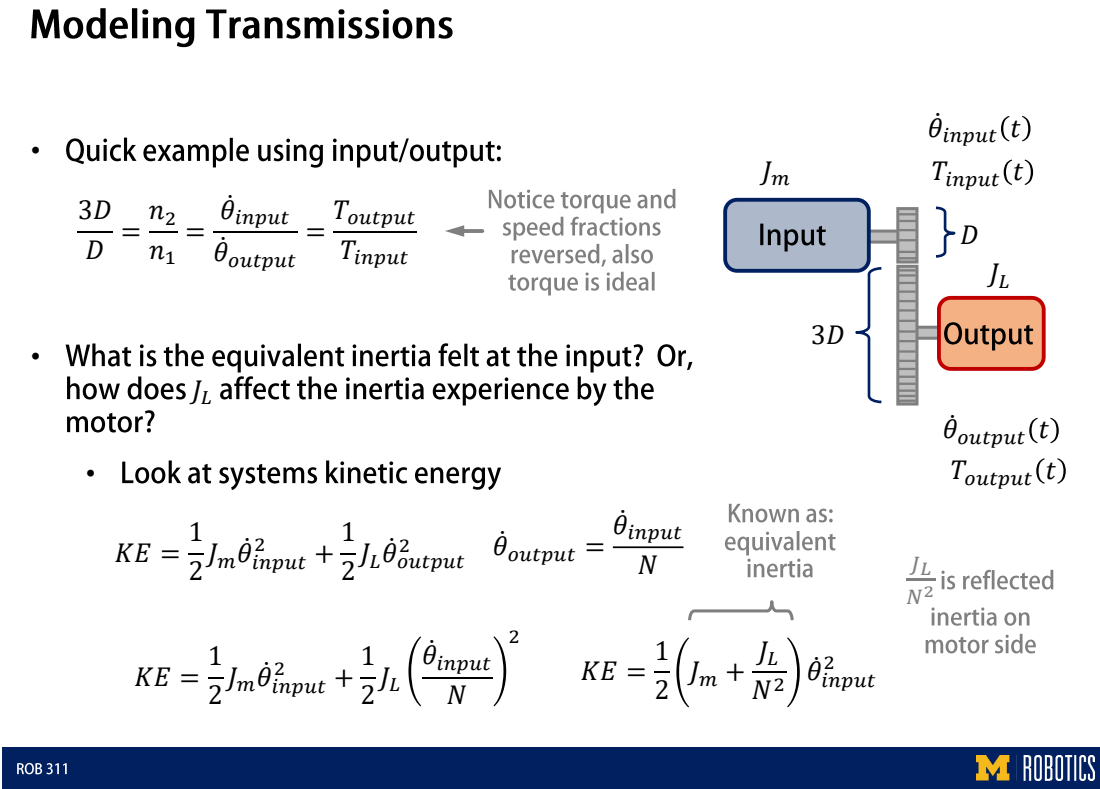
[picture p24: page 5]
Tinput t; θሶ input t; Toutput t; θሶ output t; θሶ input; θሶ output; Toutput; Tinput; Jmθሶ input; JLθሶ output; output =; θሶ input N


•••

•

•

•

•

•

vEMF(t)
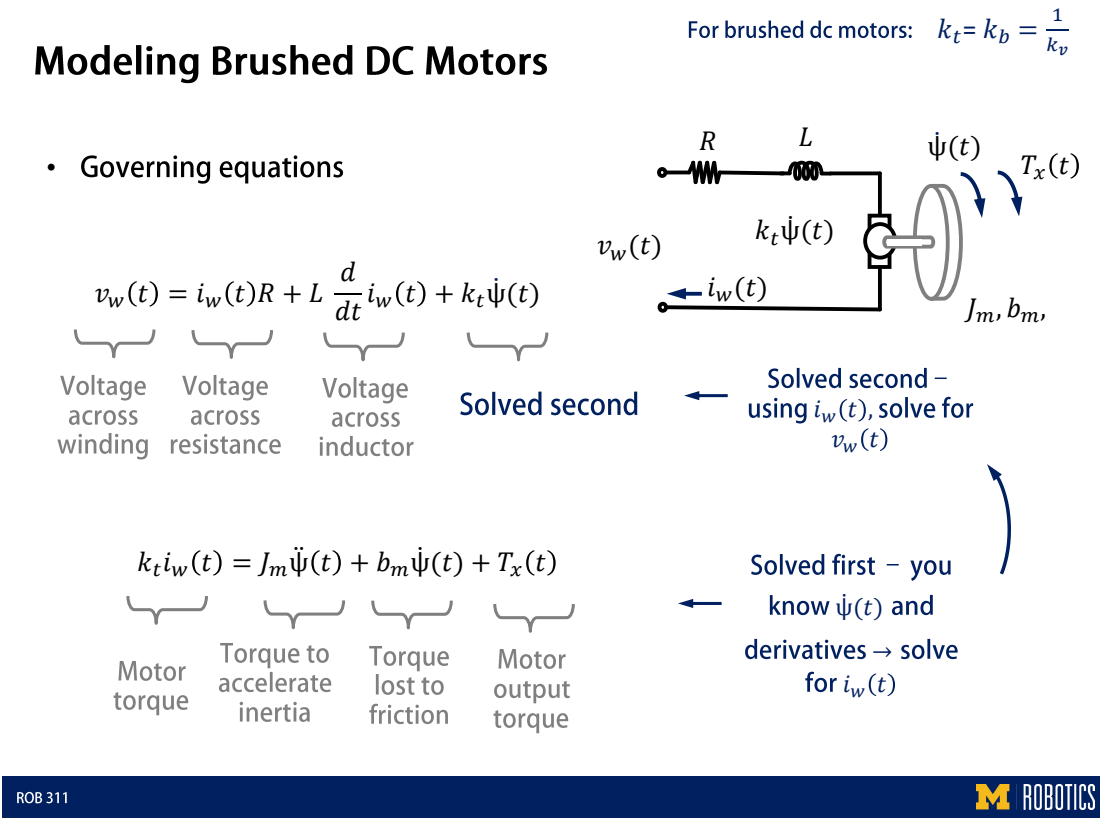
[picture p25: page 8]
d dtiw t + ktψሶ (t); ktψሶ (t)

iw t = Jmψሷ t + bmψሶ (t) + Tx t

ktψሶ (t); RTx(t) kt; + ktψሶ t; Tstall =; ∙ istall; θሶ no−load =; Tstall; −Tstall; no−load ψሶ; no−load

vw t = iw t R + ktψሶ t

d dtiw t + ktψሶ (t)

d dtiw t + ktψሶ (t)


•

•

•

- ’

•

Force = mass ∙ acceleration | F = m ∙ xሷ
Torque = Moment of inertia ∙ angular acceleration | T = J ∙ θሷ


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

•••

••••••••••

L

=

0.23

m
mA

=

1.71 kg
Ix
,

y

=

0.01 kg

m

2
Iz

=

0.017 kg

m

2

m
w

=

0.29 kg
rw

=

0.1

m
Iw

=

0.001 kg

m

2

m
k

=

0.62 kg
rk

=

0.12

m
I
k

=

0.004 kg

m

2


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
(rad

)

••

ψ
x

ψ
y

(rad

)

•

θ
x

θ
y

(rad

)

θ
x

θ
y

(rad

)

•
••

x

y

•
•


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
rkrw
(

φ

−

θ

)

−

θ

• xሶk; final = 1; xሶk; tfinal; tconstant


xሶk rk; xk = rkφ

FW2 = ma + mw ∙ g ∙ sin θ − rkφሷcos θ − γθሷ

xሶk rk; + JNψሷ+ bNψሶ; diw dt

FW2 = ma + mw ∙ g ∙ sin θ − rkφሷcos θ − γθሷ

vw = iwR + ktNψሶ + L

xሶk rk; + JNψሷ+ bNψሶ; diw dt

FW2 = ma + mw ∙ g ∙ sin θ − rkφሷcos θ − γθሷ

vw = iwR + ktNψሶ + L

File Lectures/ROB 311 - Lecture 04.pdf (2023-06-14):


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
- sudo

•


•
- /etc/startup_mailer.py
•

/etc/wpa_supplicant/wpa_supplicant-wlan0.conf
- /home/pi/rob311
- /home/pi/RPi_example_code
- /home/pi/rtplot
- /home/pi/Actuator-Package
•
- ls | ls -a
- cd DIRECTORY | DIRECTORY
- mkdir DIRECTORY | DIRECTORY
- touch FILENAME | FILENAME
- cat FILENAME | FILENAME
- nano FILENAME | FILENAME
- ping www.google.com
- Sudo shutdown now or sudo reboot


•

•

•
raspi-config

•

•


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

••

•••


L

=

0.23

m

mA

=

1.71 kg
Ix
,

y

=

0.01 kg

m

2
Iz

=

0.017 kg

m

2

m
w

=

0.29 kg
rw

=

0.1

m
Iw

=

0.001 kg

m

2

m
k

=

0.62 kg
rk

=

0.12

m
I
k

=

0.004 kg

m

2


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
(rad

)

••

ψ
x

ψ
y

(rad

)

•

θ
x

θ
y

(rad

)

θ
x

θ
y

(rad

)

•
••

x

y

•
•


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
rkrw
(

φ

−

θ

)

−

θ

• xሶk; final = 1; xሶk; tfinal; tconstant


xሶk rk; xk = rkφ; xkሶ

FW2 = ma + mw ∙ g ∙ sin θ − rkφሷcos θ − γθሷ

xሶk rk; + JNψሷ+ bNψሶ; diw dt; xሶk

FW2 = ma + mw ∙ g ∙ sin θ − rkφሷcos θ − γθሷ

vw = iwR + ktNψሶ + L

xሶk rk; + JNψሷ+ bNψሶ; diw dt; xሶk

FW2 = ma + mw ∙ g ∙ sin θ − rkφሷcos θ − γθሷ

vw = iwR + ktNψሶ + L

mla; φሷ+ bφሶ +; mgl cos θ ηN; v = iwR + ktNθሶ + L; diw dt; Nθሷ+ bNθሶ +

Goal: Determine the motor current, voltage,
torque, and speed for the task. You will need
to begin with a motor from the provided
spreadsheet. The input (theta) has been
provided in a .mat file that will load
automatically from a starting script provided.

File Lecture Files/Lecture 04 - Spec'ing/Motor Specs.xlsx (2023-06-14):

Motor name | T-motor U8 KV100 | T-motor U3 KV700 | T-motor U5 KV400 | T-motor U7 V2.0 KV280 | T-motor U11 KV90 | T-motor U11 II KV120 | T-motor U13 KV85 | T-motor U13 II KV130 | T-motor U15 II KV80 | T-motor U8 KV135 | T-motor U8 KV170 | T-motor U8 PRO KV100 | T-motor U8 PRO KV135 | T-motor U8 PRO KV170 | T-motor U8 II KV85 | T-motor U8 II KV100 | T-motor U8 II KV150 | T-motor U8 II KV190 | T-motor U8 Lite KV85 | T-motor U8 Lite KV100 | T-motor U8 Lite KV150 | T-motor U8 Lite KV190 | T-motor U10 KV80 | T-motor U10 KV100 | T-motor U10 II KV100 | T-motor U12 KV85 | T-motor U12 KV90 | T-motor U12 KV100 | T-motor U12 II KV120 | T-motor P60 KV170 | T-motor P60 KV340 | T-motor P80 KV100 | T-motor P80 KV120 | T-motor P80 KV170 | T-motor P80 III Pin KV100 | T-motor P80 III Pin KV120 | T-motor P80 III Without Pin KV100 | T-motor P80 III Without Pin KV120 | T-motor Antigravity MN4004 KV300 | T-motor Antigravity MN4004 KV400 | T-motor Antigravity MN4006 KV380 | T-motor MN6007 KV160 | T-motor MN6007 KV320 | T-motor MN7005 KV115 | T-motor MN7005 KV230 | T-motor MN1005 KV90 | T-motor MN501-S KV240 | T-motor MN501-S KV300 | T-motor MN501-S KV360 | T-motor MN505-S KV320 | T-motor MN505-S KV380 |
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

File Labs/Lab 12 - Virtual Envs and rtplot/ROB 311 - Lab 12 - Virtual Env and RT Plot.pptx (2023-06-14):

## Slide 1


Robotics 311 : How to build robots and make them move

Prof. Elliott Rouse
GSI Yves Nazon MS
Fall 2022

Photo credit: Brenda Ahearn / U-M CoE

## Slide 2

ROB 311 – Lab 12

- Today, we will learn about virtual environments and real time plotting!

alt text
Anaconda | The World's Most Popular Data Science Platform

ROB 311

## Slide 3

ROB 311 – rtplot

- About rtplot
  - Real time plotter
  - Uses socket protocols for communication between devices
    - Socket communication is a network (wireless) form of communication
    - Clients send info to servers


ROB 311

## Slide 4

ROB 311 – Virtual Environments

- What is a virtual environment
  - A file structure that runs a version of python with specific dependencies and packages
- Why use a virtual environment
  - An easy way to ensure you have the correct packages for a specific project
  - Avoid many issues
    - Contaminating native python versions
    - Dependency conflicts
    - Need for admin access

ROB 311

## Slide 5

ROB 311 – Anaconda

- About anaconda
  - Open source distribution of python (and R)
  - Made to assist with package management and usage for multiple projects
  - OS agnostic

Anaconda Navigator — Anaconda documentation

ROB 311

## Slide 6

ROB 311– Todays Lab

- Create a virtual environment using anaconda
- Use the real time plotter to plot ballbot states
  - ROB311_rtplot_demo.py has example syntax

ROB 311

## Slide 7

ROB 311 – Creating Virtual Environment with Anaconda

- Download Anaconda
  - https:// (https://www.anaconda.com/products/distribution)www.anaconda.com/products/distribution
  - Follow download prompts
    - OS specific download assistance found here: https://docs.anaconda.com/anaconda/install/ (https://docs.anaconda.com/anaconda/install/)
    - Conda commands cheat sheet: https://docs.conda.io/projects/conda/en/4.6.0/_downloads/52a95608c49671267e40c689e0bc00ca/conda-cheatsheet.pdf (https://docs.conda.io/projects/conda/en/4.6.0/_downloads/52a95608c49671267e40c689e0bc00ca/conda-cheatsheet.pdf)
- Open terminal (Mac/Linux) or use anaconda navigator → CMD prompt (windows)

ROB 311

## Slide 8

ROB 311 – Creating Virtual Environment (Cont.)

- Check if conda is installed on your path
  - Conda –V
- Check if Conda is up to date
  - Conda update conda
- Create a Virtual Environment
  - Ex: conda create --name sample_venv python=3.8
  - Make sure python version is 3.9
- Activate the environment
  - conda activate sample_venv
- Deactivate the above environment once your work is done
  - conda deactivate

ROB 311

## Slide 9

ROB 311– Using rtplot

- Clone rtplot repo from git
  - https://github.com/jmontp/rtplot (clone repo first!)
  - Follow instructions for installation and downloading dependencies
    - Do this within virtual environment!
  - Replace repo version of server.py with canvas version
  - Check correctness using example_code.py

ROB 311

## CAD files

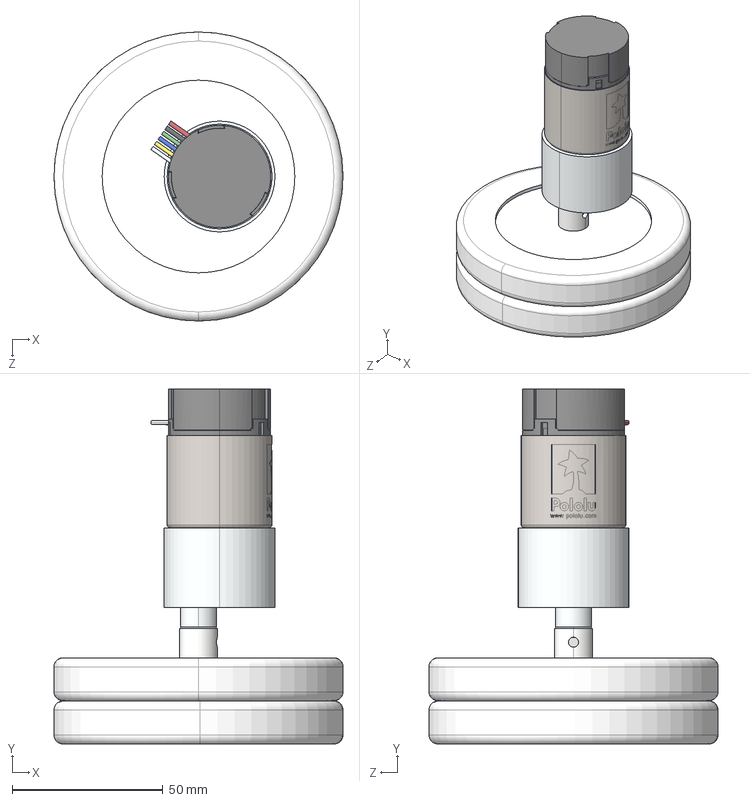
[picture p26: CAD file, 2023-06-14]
Labs/Lab 03 - Design Files/STEP files for provided parts/motor-wheels-subassembly.STEP
96.0 x 117.9 x 96.0 mm
37d-gearmotor-100-131-150-encoder.step
BB311-Motor-Coupler v18.step
omni-wheel-100mm x 2

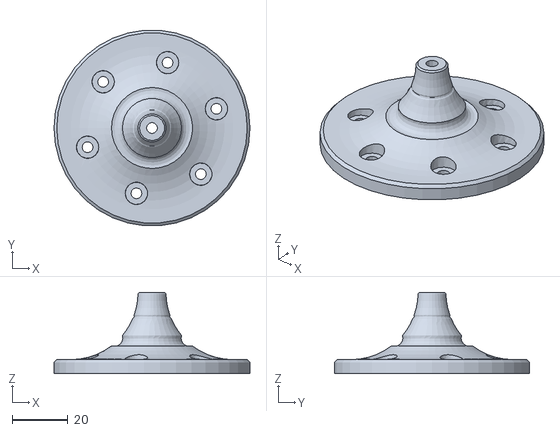
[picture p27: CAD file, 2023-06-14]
HWs/HW 2/ROB311_Ball-Bot_Leash_Attachment.STL
70.0 x 69.8 x 29.0

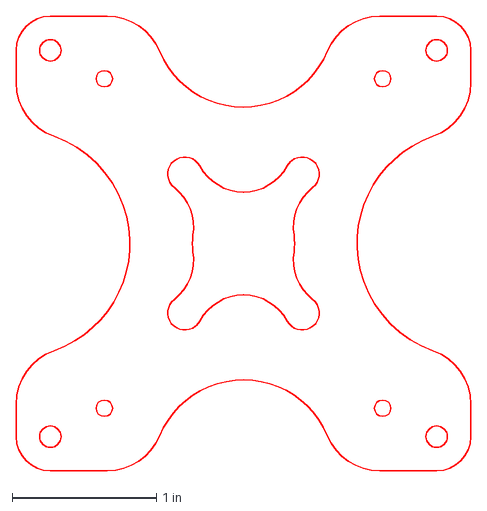
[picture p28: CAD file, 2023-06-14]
Labs/Lab 03 - Design Files/pico-plate-RED.dxf
3.15 x 3.15 in

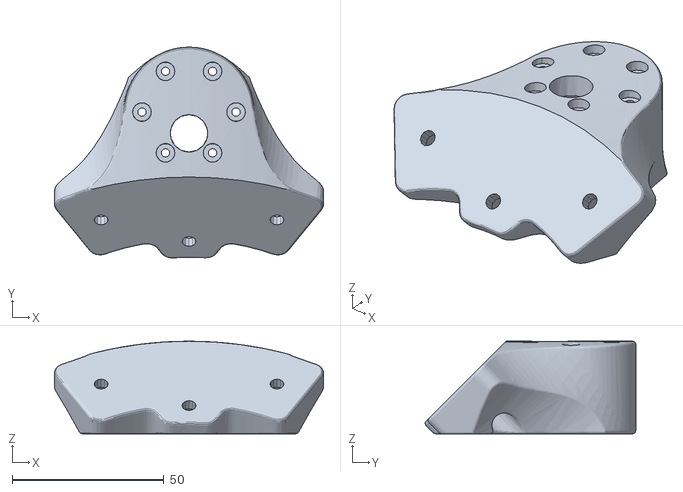
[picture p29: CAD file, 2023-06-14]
Labs/Lab 03 - Design Files/motor-mount-example.STL
88.6 x 69.4 x 30.5

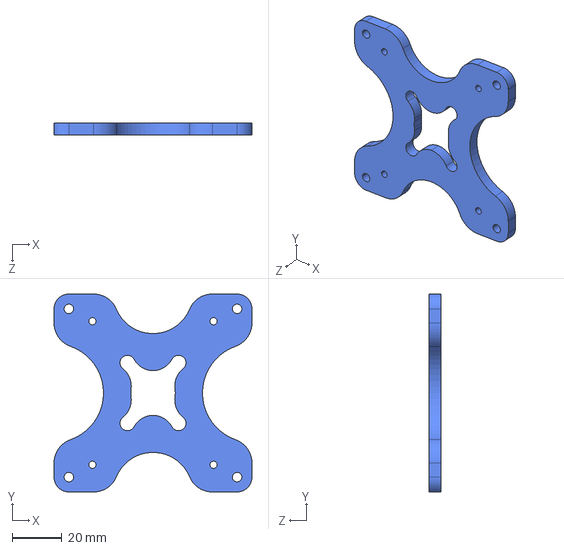
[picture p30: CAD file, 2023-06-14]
Labs/Lab 03 - Design Files/STEP files for provided parts/pico-plate-v3.STEP
80.0 x 80.0 x 4.76 mm

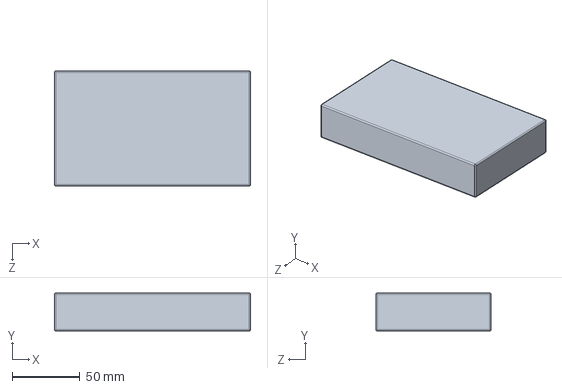
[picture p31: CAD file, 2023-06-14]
Labs/Lab 03 - Design Files/STEP files for provided parts/battery.STEP
145.0 x 28.0 x 85.0 mm

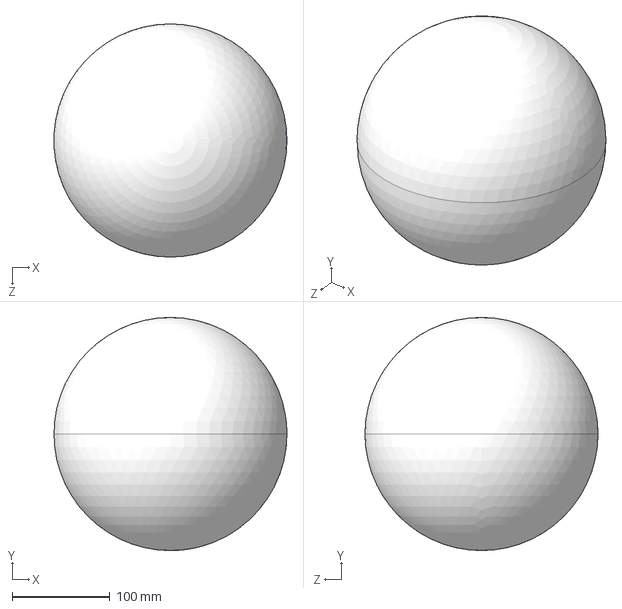
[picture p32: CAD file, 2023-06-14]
Labs/Lab 03 - Design Files/STEP files for provided parts/basketball-size-7.STEP
238.3 x 238.5 x 238.5 mm

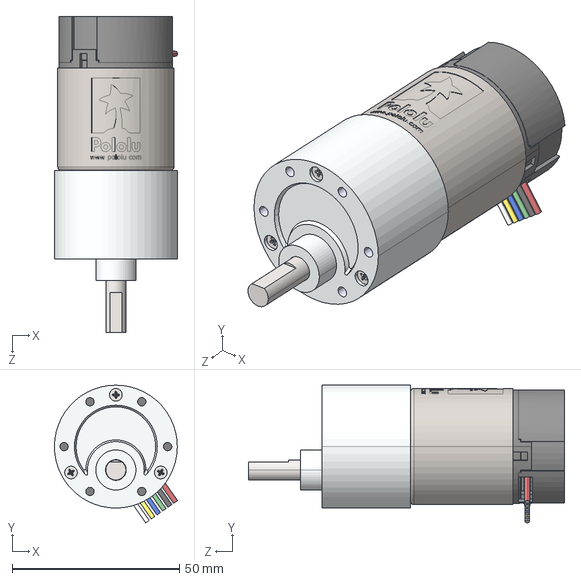
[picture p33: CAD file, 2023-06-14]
Labs/Lab 03 - Design Files/STEP files for provided parts/motor.step
36.9 x 41.2 x 94.6 mm

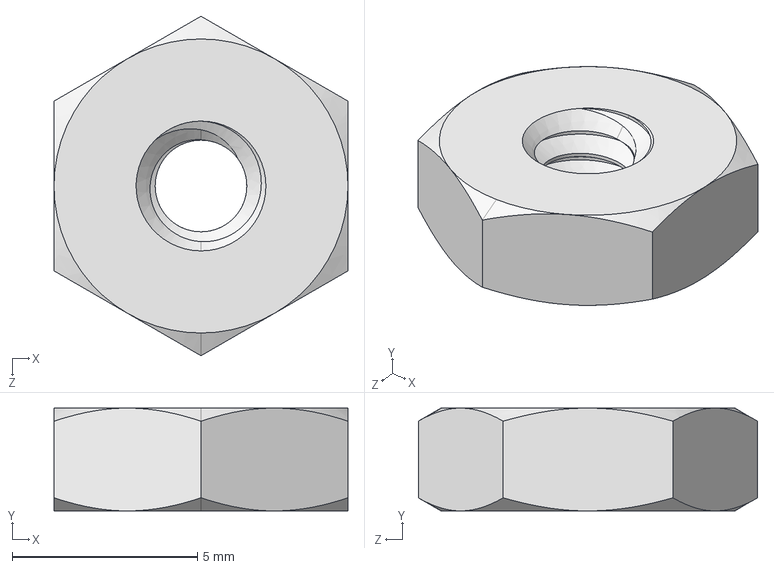
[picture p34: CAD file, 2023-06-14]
Labs/Lab 03 - Design Files/STEP files for provided parts/96537A130_18-8 Stainless Steel Hex Nut.STEP
7.94 x 2.78 x 9.17 mm

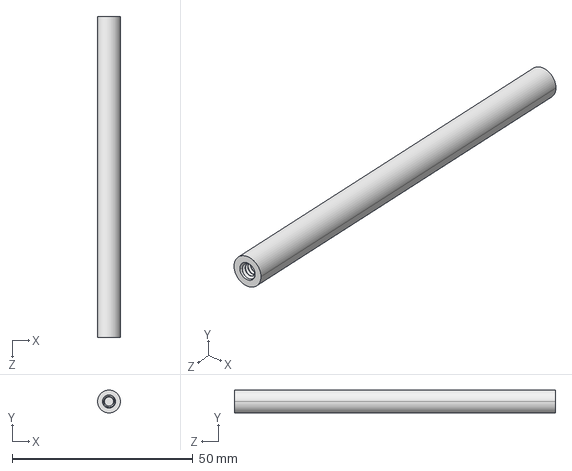
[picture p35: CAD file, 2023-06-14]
Labs/Lab 03 - Design Files/STEP files for provided parts/91125A039_Female Threaded Round Standoff.STEP
6.35 x 6.35 x 88.9 mm

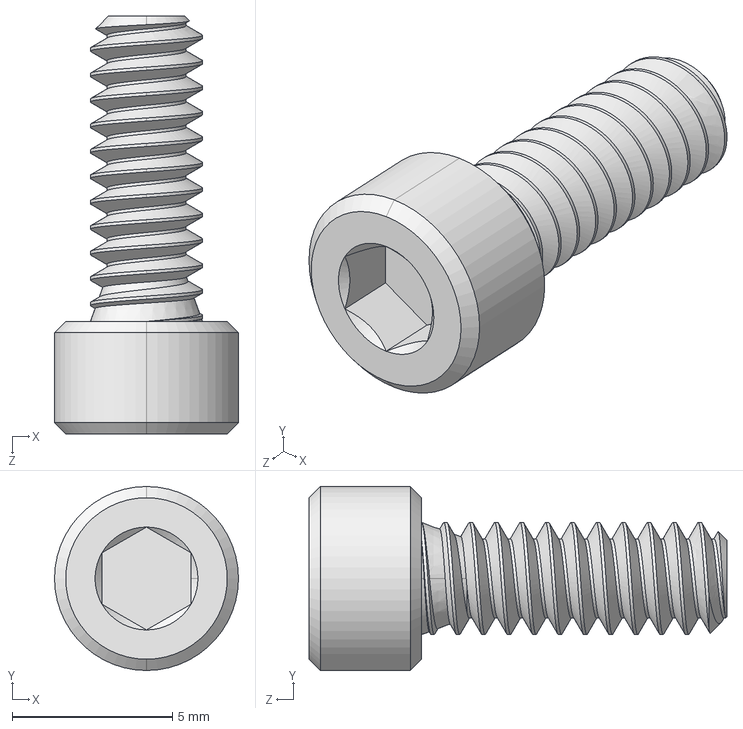
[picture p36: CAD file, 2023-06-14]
Labs/Lab 03 - Design Files/STEP files for provided parts/91251A146_Black-Oxide Alloy Steel Socket Head Screw.STEP
5.74 x 5.74 x 13.0 mm

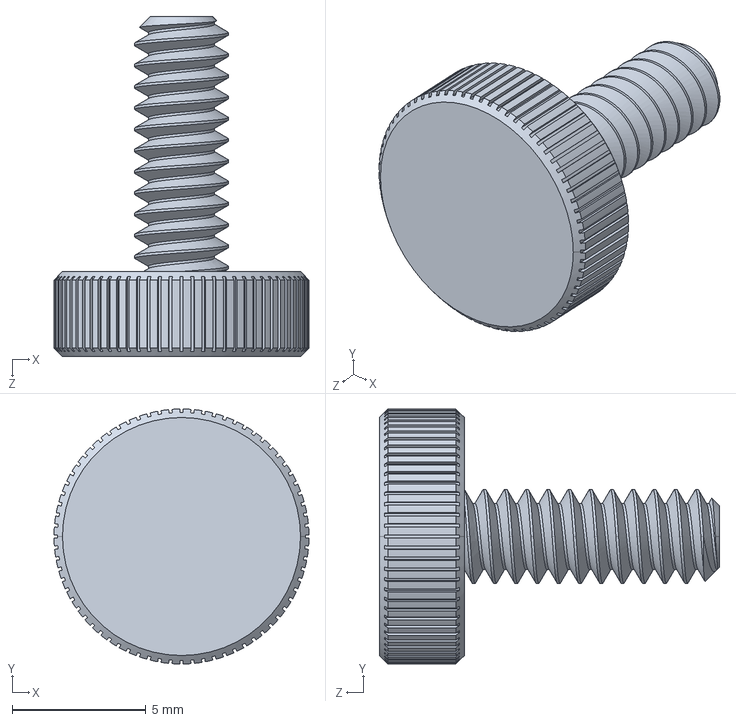
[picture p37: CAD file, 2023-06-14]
Labs/Lab 03 - Design Files/STEP files for provided parts/94955A010_Low-Profile Nylon Thumb Screw.STEP
9.52 x 9.52 x 12.7 mm

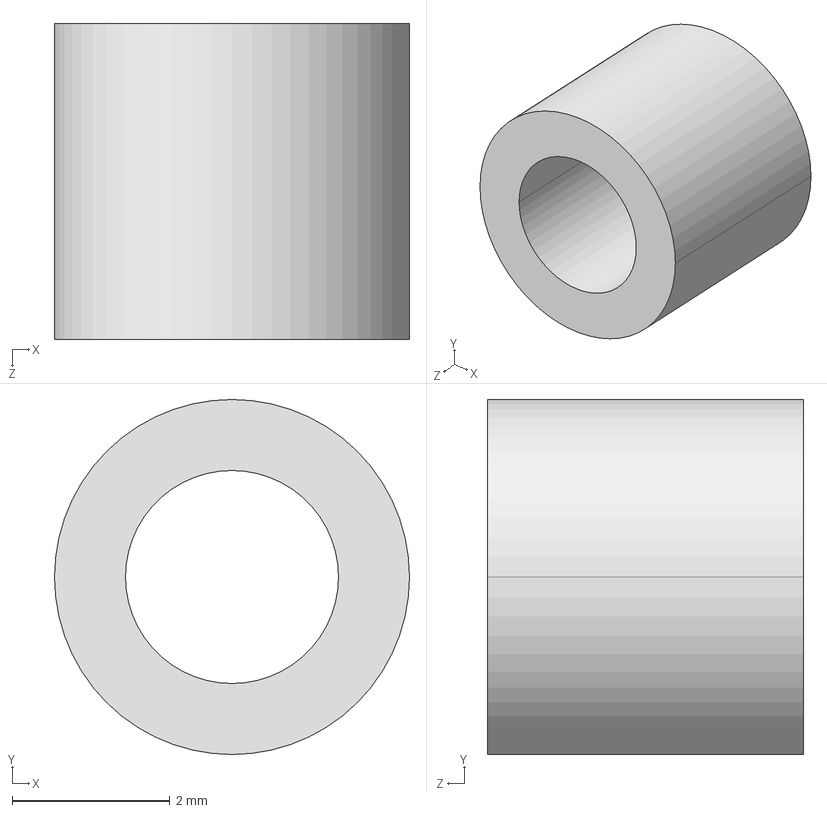
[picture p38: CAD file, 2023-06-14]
Labs/Lab 03 - Design Files/STEP files for provided parts/94669A096_Aluminum Unthreaded Spacer.STEP
4.50 x 4.50 x 4.00 mm

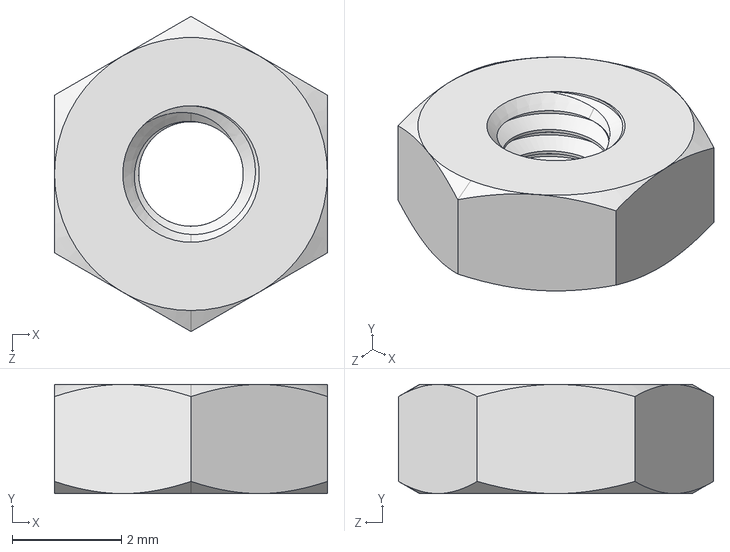
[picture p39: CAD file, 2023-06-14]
Labs/Lab 03 - Design Files/STEP files for provided parts/90592A080_Steel Hex Nut.STEP
5.00 x 2.00 x 5.77 mm

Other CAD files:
Labs/Lab 03 - Design Files/motor-mount-skeleton.SLDPRT
Labs/Lab 03 - Design Files/base-plate-skeleton.SLDPRT
Labs/Lab 03 - Design Files/STEP files for provided parts/93945K101_Vibration-Damping Sandwich Mount with Stud and Insert.STEP
Labs/Lab 03 - Design Files/STEP files for provided parts/94645A101_High-Strength Steel Nylon-Insert Locknut.STEP
Labs/Lab 03 - Design Files/STEP files for provided parts/91290A150_Alloy Steel Socket Head Screw.STEP
Labs/Lab 03 - Design Files/STEP files for provided parts/91864A019_Black-Oxide Alloy Steel Socket Head Screw.STEP
Labs/Lab 03 - Design Files/STEP files for provided parts/93330A472_Female Threaded Round Standoff.STEP
Labs/Lab 03 - Design Files/STEP files for provided parts/93705A813_18-8 Stainless Steel Thread-Locking Socket Head Screw.STEP
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

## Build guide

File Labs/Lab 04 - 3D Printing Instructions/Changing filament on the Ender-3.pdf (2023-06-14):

# Changing filament on the Ender-3

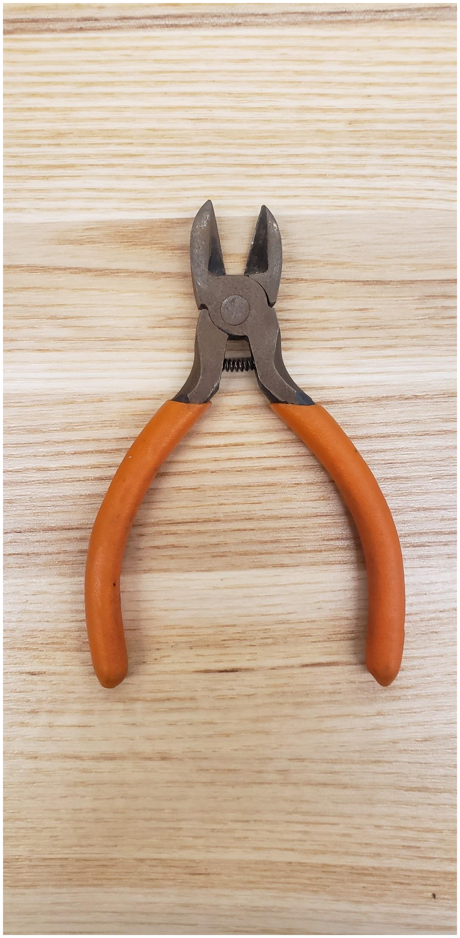
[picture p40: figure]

# Tools needed

## - Side cutters/flush cuts - Tweezers

# 1. Heat up the hot end

Using the control panel, select the control option. Scroll down to and select temperature on the menu. Select nozzle temperature and turn it up to about 200 degrees Celsius.

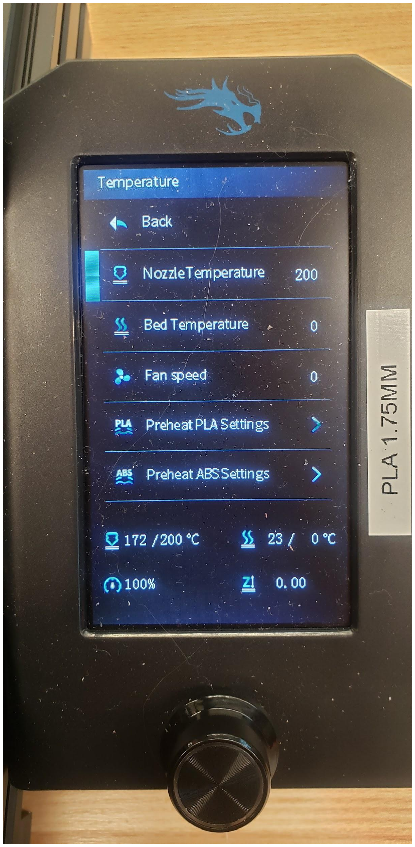
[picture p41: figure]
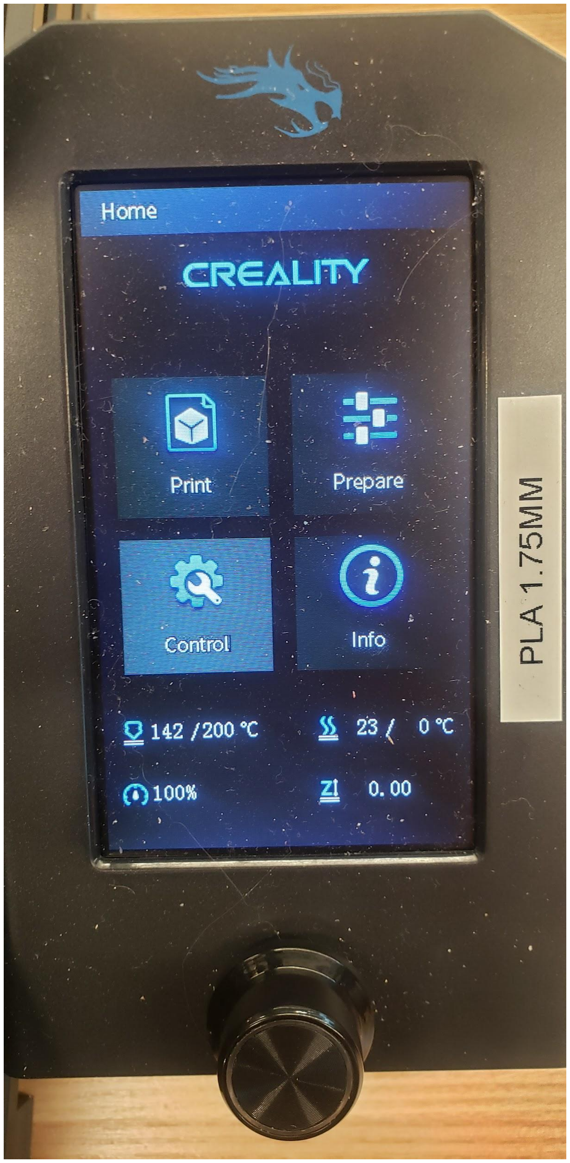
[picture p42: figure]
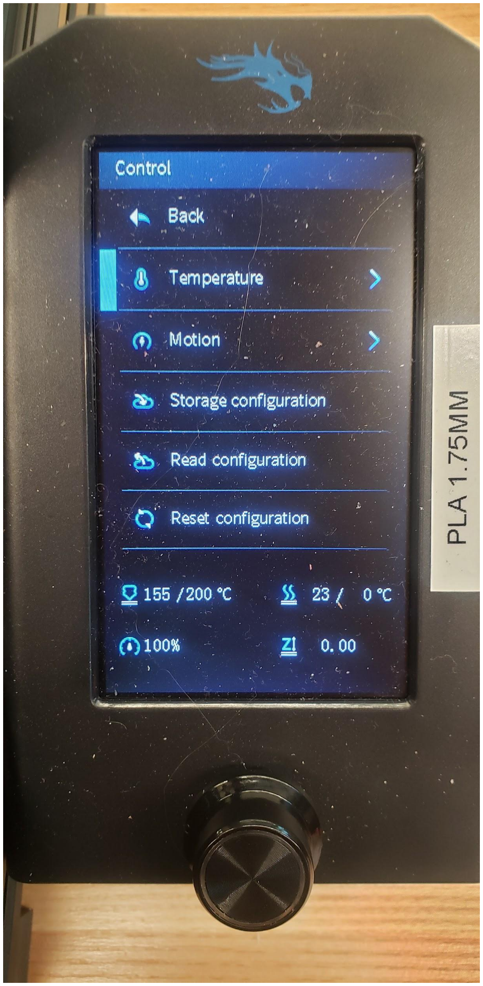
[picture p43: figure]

# 2. Remove any debris from the nozzle

While the nozzle is heating, CAREFULLY use
the tweezers to remove any excess and burnt filament from the nozzle.

# 3. Back the filament out

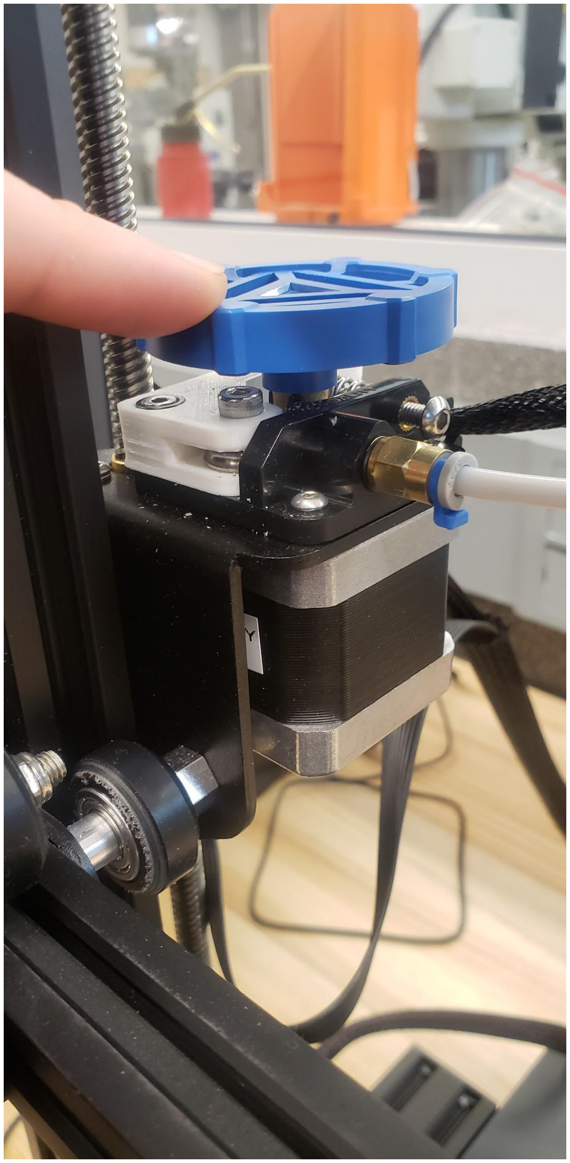
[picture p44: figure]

Using the blue knob on top of the extruder the filament can be removed. By turning the knob clockwise back the filament out while also keeping the spool of filament taut in order to prevent snags.

# 4. Remove old filament and prep new spool to be loaded

1. Remove the old spool of filament and replace it with a
new on. *ALWAYS BE SURE TO CHECK MATERIAL AND FILAMENT DIAMETER*
2. Find the end of the filament on the new spool, using a set of side cutters cut the end of the filament at about a 45 degree angle

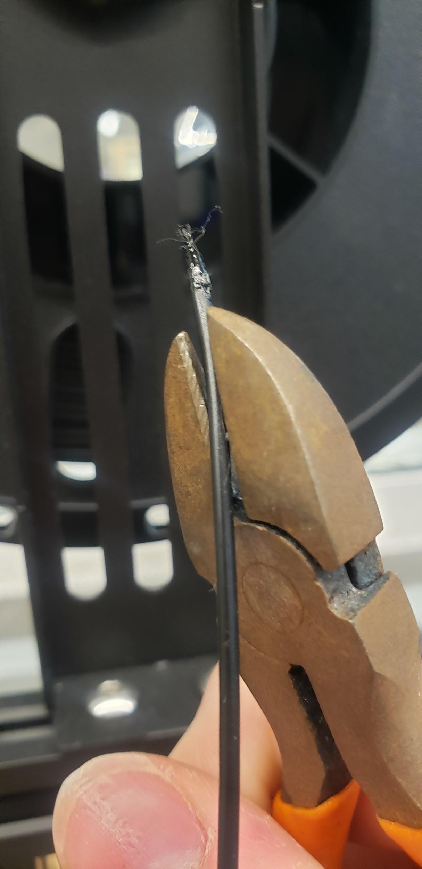
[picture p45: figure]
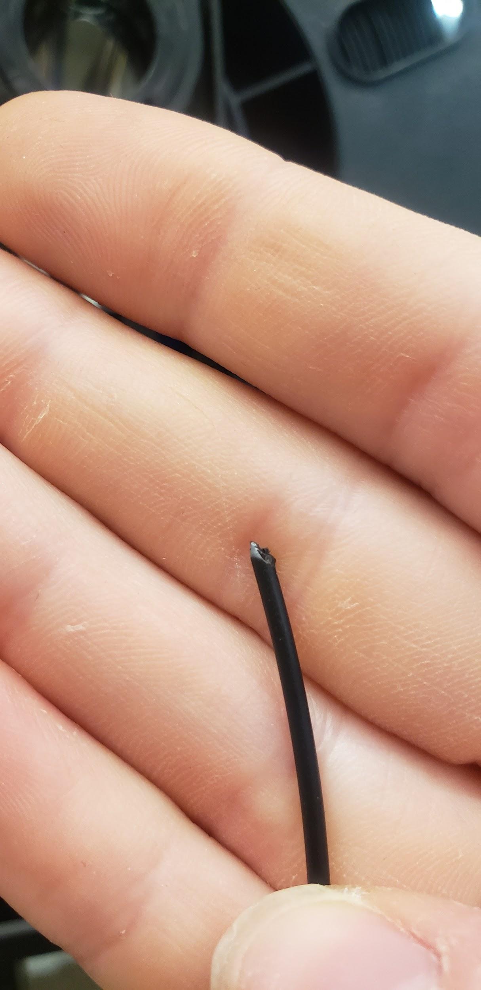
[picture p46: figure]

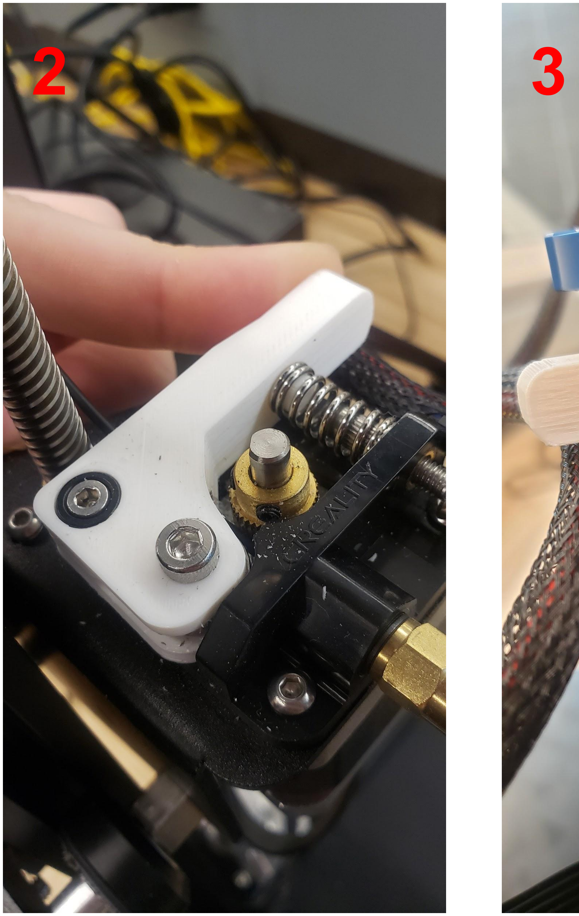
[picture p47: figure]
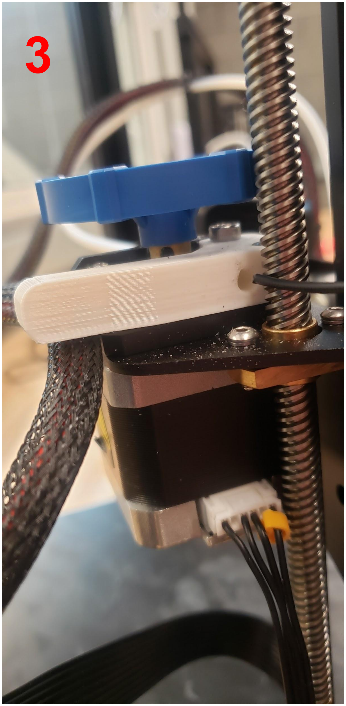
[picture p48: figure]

1. Remove the blue knob from the top of the extruder
2. Press the extruder arm to compress the spring and release tension on the extruder wheel
3. Pass the newly cut filament through the hole on the side of the extruder arm
4. Pass the filament past the extruder wheel into the hole leading to the bowden tube *You may have to bend and straiten the filament to aid in this process
5. Release pressure on the extruder arm and replace the knob
6. Turn the knob counterclockwise to load the filament
7. Continue doing this until the filament reaches the hot end and starts extruding
8. Manually extrude some filament

# 5. Load the new filament

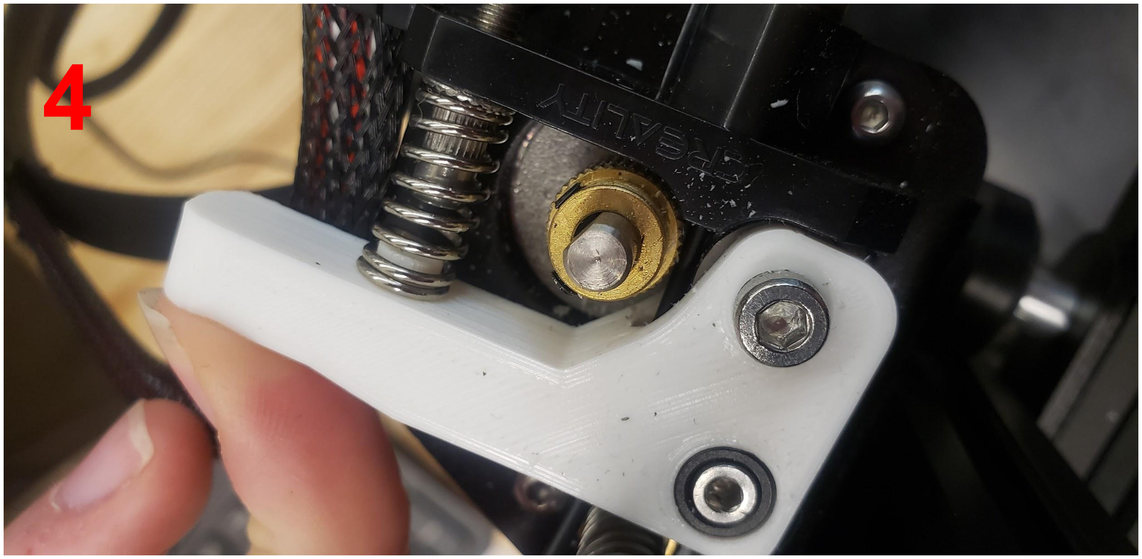
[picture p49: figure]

# 6. You did it!

At this point I like to run a quick, small test print to make sure everything is working properly but thats it otherwise!

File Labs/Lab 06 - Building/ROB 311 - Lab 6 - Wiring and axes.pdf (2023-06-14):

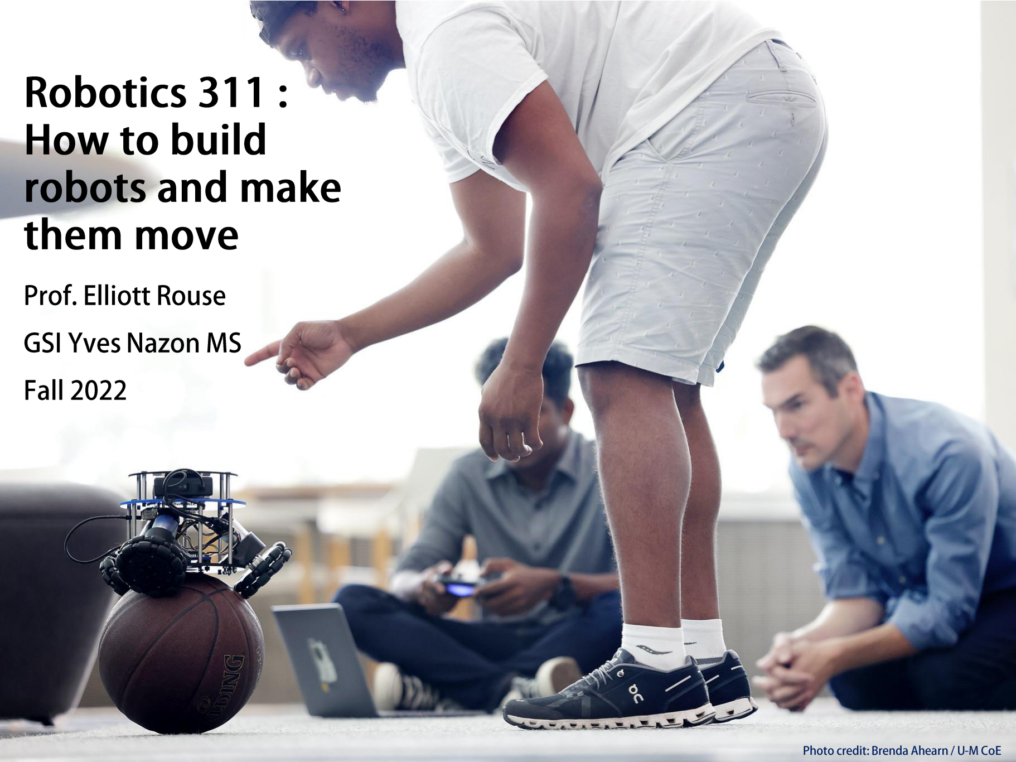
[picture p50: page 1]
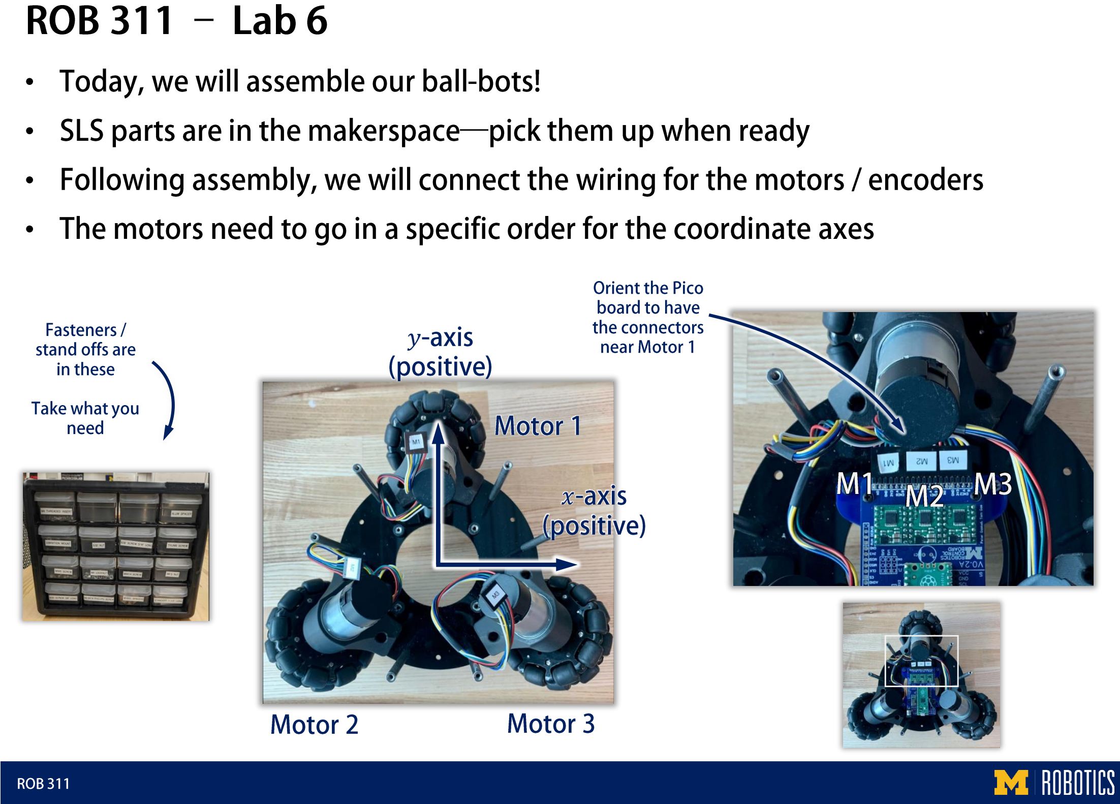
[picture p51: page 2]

••••

x

y

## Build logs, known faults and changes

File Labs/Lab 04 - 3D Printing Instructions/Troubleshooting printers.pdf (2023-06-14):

# Troubleshooting printers

# Intro

# While printers normally function fine, there is a wide variety of things that can happen that interfere with day to day printing. Here are some along with how to

identify them as well as some potential solutions.

# Heat creep

## What is it? Heat creep specifically describes how heat travels

(sneakily) up the hot end and melts filament too early,

## before the melt zone.This problem can manifest mid-print or after a print (during cooling) but usually occurs and is noticed in the middle of a print when temperatures are

highest. (https://www.reddit.com/r/MPSelectMiniOwners/comments/6aok90/what_are_some_signs_of_heat_creep/)

## How do I know? You can see evidence of heat creep when your 3D printed part looks only half-complete with a fuzzy top. You can also detect heat creep when you pull your filament out and

there’s an air bubble.

## What causes it?

## - Hot end temperature is too high

## - Cooling fan is broken, not working properly, or

## isn't cooling the hot end enough

## - Too high retraction length

## - Heat sink is dusty

## - Printing speed is too low

## - Filament is in the hot end for too long

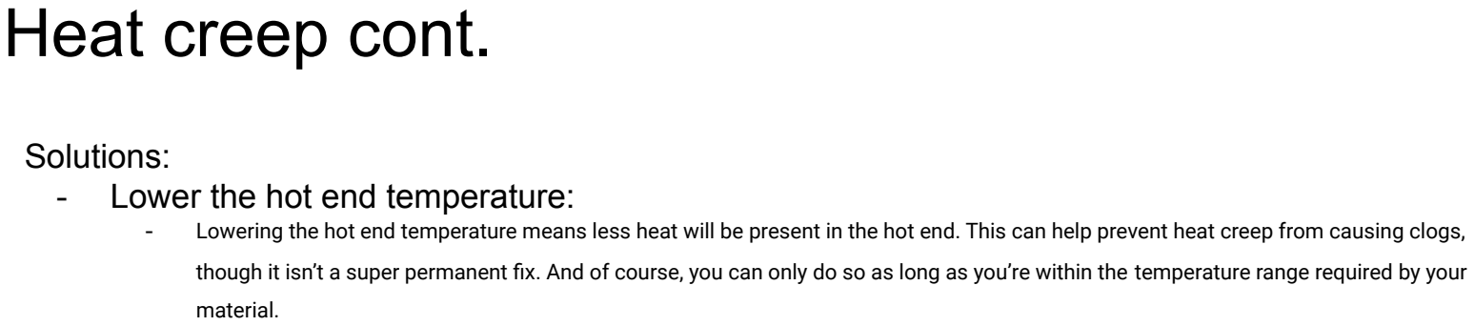
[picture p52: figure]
Heat creep cont.; Solutions: - Lower the hot end temperature:; material.

- Lowering the hot end temperature means less heat will be present in the hot end. This can help prevent heat creep from causing clogs,

though it isn’t a super permanent fix. And of course, you can only do so as long as you’re within the temperature range required (https://all3dp.com/2/the-best-printing-temperature-for-different-filaments/) by your

## - Increase Fan speed:

- First, you should set the fan to 100% speed and make sure that the heat creep stops occurring. After it does, lower the speed in increments of 10% if you experience warping, cracking, or other cooling-related print issues.

## - Increase printing speed:

- You should use the same temperature with a speed of 10-15 mm/s faster than what you normally use. Consider adjusting your printing speed in increments of 2-5 mm/s until you find the right mix between proper melting and preventing under-extrusion.

## - Replace the hot end: (Last resort)

- Though all-metal hot ends are often seen as upgrades over others, they could act as a heat creep catalyst if other conditions are resulting in an excess of heat. In this case, you might consider using a PTFE-lined hot end.
- A PTFE-lined hot end, along with the removable PTFE tube, provides more insulation for the filament and preserves the sub-melting temperature until the filament hits the melt zone. This solution prevents heat from getting into the hot end but doesn’t stop the problem.

Heat creep cont.

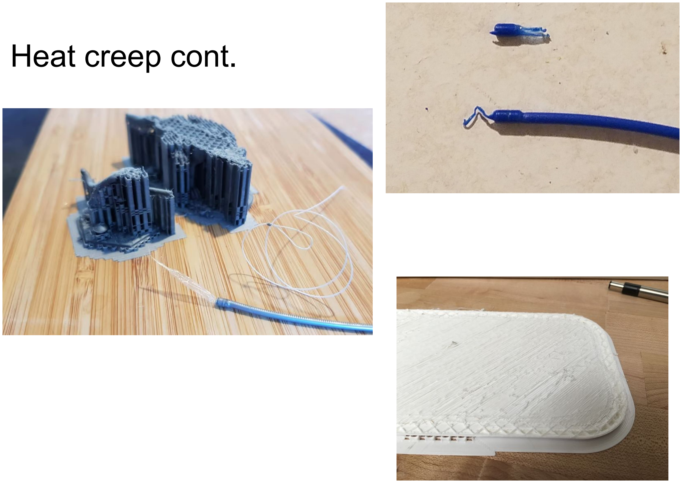
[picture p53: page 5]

# Under extruding

## What is it? Under-extrusion is the term given to the printer not

supplying sufficient material for the print.

## Under-extrusion has many telltale signs — most significantly thin layers, unwanted gaps and even missing layers entirely

What causes it? There are several possible causes. First, the diameter of the filament used does not match the diameter set in the slicing software. Secondly, the amount of material that is extruded is too low because of faulty slicer software settings. Alternatively, the flow of the material through the extruder is restricted by debris in the nozzle

## How do I know? Layers will look thin and wimpy, layers will also sometimes

have a sputtering look to them.

Under extruding cont.

## Solutions: - Check the filament/nozzle diameter

- Start with the simplest issue, have you set the correct filament diameter in the slicing software. If you’re unsure about the diameter the value along with the recommended temperature is usually printed on the box.

## - Measure the filament

- If you’re still not getting the results you want and filament flow is the issue, then use a set of calipers to double check the filament diameter. You should be able to tweak the filament diameter settings accurately in the slicer software settings.

## - Check the hot end for debris

- After printing, most printers will lift the printhead away from the print base. Quickly check that the nozzle is clear from a build up of filament and dirt.

## - Adjust the extrusion multiplier

- If there is no mismatch between actual filament diameter and the software setting, then then the extrusion multiplier (also referred to as the flow rate or flow compensation) may be too low. Each slicer application will handle this slightly differently but the principle is to increase this value in steps of 5% until you see the problem is gone.

Under extruding cont.

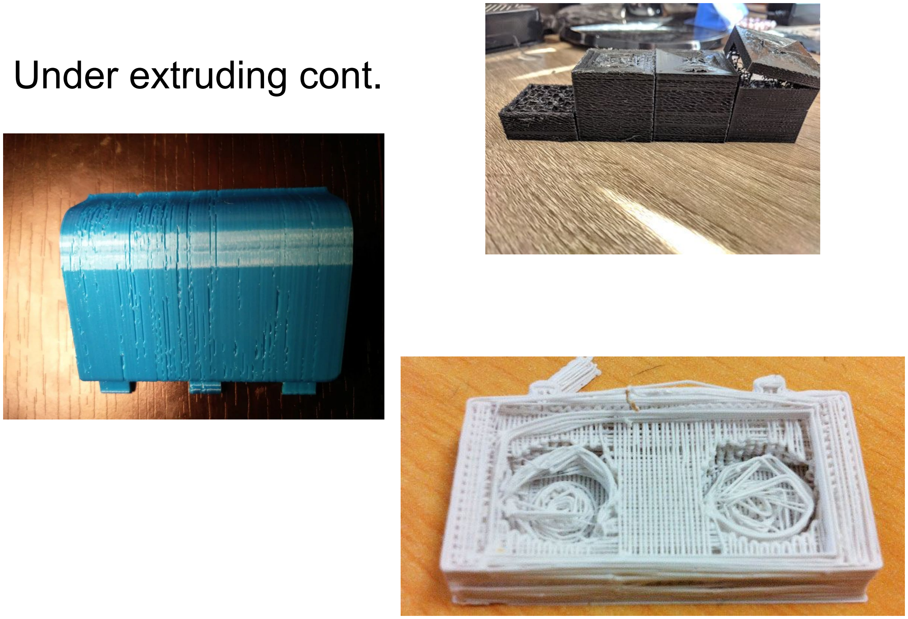
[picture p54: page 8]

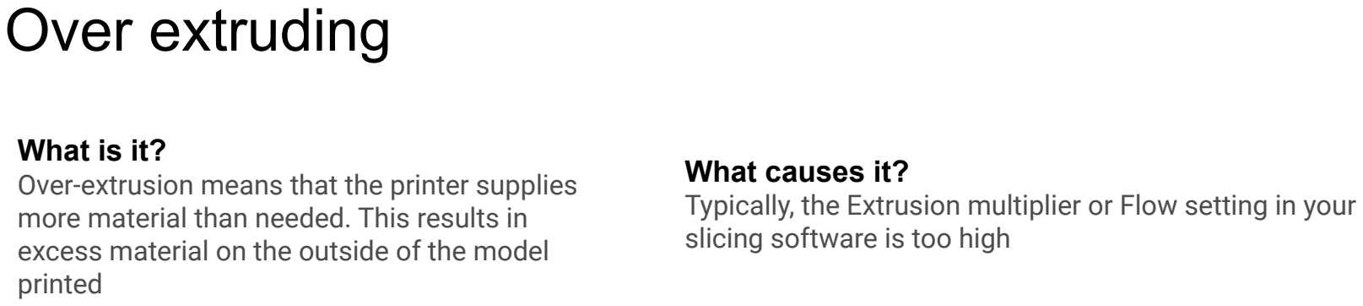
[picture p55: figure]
Over extruding; What is it?; printed; What causes it?; slicing software is too high

## Over-extrusion means that the printer supplies more material than needed. This results in excess material on the outside of the model

## Typically, the Extrusion multiplier or Flow setting in your

## How do I know? The print will be stringy and droopy

Over extruding cont.

## Solutions: - Check you have the right extrusion multiplier settings

- Open your slicer software and check that you have the correct Extrusion multiplier selected

## - Decrease your flow settings

- If that all looks correct then decrease the Flow setting in your printer’s software.

Over extruding cont.

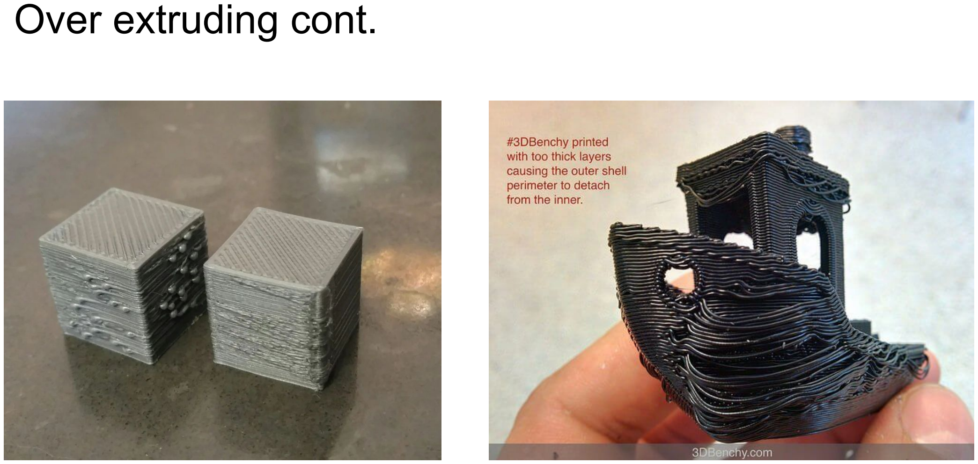
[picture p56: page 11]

# Loud beeping noise and a black screen

## What is it? When the printer is turned on, the menu screen will be black and a loud beeping sound

will continuously yell at you.

## What causes it? Outdated, corrupt or improper firmware flashed onto the printer

## How will I know?

There will be an obnoxiously loud continuous beeping sound and the screen will be black.

Loud beeping noise and black screen cont.

## Solutions

-Format an SD card and load the .bin file below to it (can be found in the FRB drive additionally). Install the SD card into the printer and turn the printer on. Wait a few seconds and the printer will load the firmware on and refresh its system.

## https://drive.google.com/file/d/188TpLAu2__Tdoh19C_zd3Y5HPfy-6gUk/view?usp=sharing

# The nozzle is too close to the bed

## What is it? Inexplicably, despite loading the filament and the print head moving without a hitch, little to no filament is

depositing on the print bed.

## What causes it? Quite simply, your nozzle may be too close to the print bed. If you’ve somehow tuned your print bed to mere microns from your nozzle opening, it’s unlikely the melted filament has room to escape. At best your print will be missing its first layers, and have a higher chance

of not sticking once the filament does extrude. At worst, you’ll cause a backup of melted filament in your hot end, possibly leading to a blockage/clog.

## How do I know? During printing, especially during the first few layers either extremely thin/transparent or no filament will extrude from the nozzle

Nozzle is too close cont.

Solutions;

## - Adjust the Z-axis

- Just raising the height of the nozzle slightly can often help. Most 3D printers in their system settings will allow you to set a Z-axis offset. To raise your nozzle away from the print bed you’ll need to increase the offset into the positive value. This also works for the reverse, with a negative offset helping to address your prints not sticking to your bed. Be careful though, too high of an offset and it

## won’t stick to the platform

## - Lower the print bed

- Alternatively if your printer allows for it, you can achieve the same effect by lowering your print bed. This is the more troublesome fix though, as it requires you to re-calibrate and level the bed for even prints.

Nozzle is to close cont.

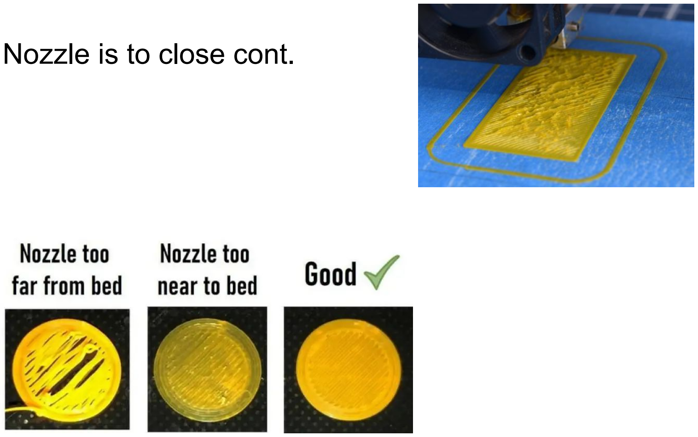
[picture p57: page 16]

# Warping

## What is it? At the base of the model, the print bends upwards until it’s no longer level with the print platform. This can also result in horizontal cracks in upper parts and cause your print to

come unstuck from the print bed.

## What causes it? Warping is common as it’s caused by a natural characteristic of the plastic. As the ABS or PLA filament cools it starts to contract very slightly; the problem of

warping arises if the plastic is cooled too quickly.

## How will I know? Corners at the base of the print will be lifting

Warping cont.

## Solutions: - Add an/more adhesive to the print bed

- If you still find your print lifting at the edges then apply a tiny amount of stick glue evenly on the bed to increase adhesion

## - Level the print bed

- Print platform calibration can be another cause, run through the calibration process to check that the bed is level and nozzle height is correct.

## - Increase contact

- Increasing the contact between the model and bed is an easy fix and most print software has the option to add rafts or platforms.

## - Adjust advanced temperature settings

- If all else fails then you’ll need to take a look at your advanced print settings both on your printer and in your print software. Try increasing the print bed temperature by increments of 5 degrees. In the slicer software take a look at the fan cooling, this is usually set so the cooling fans switch to full power at a height of around 0.5mm, try extending this to 0.75 to give the base layers a little more time to cool naturally.

Warping cont.

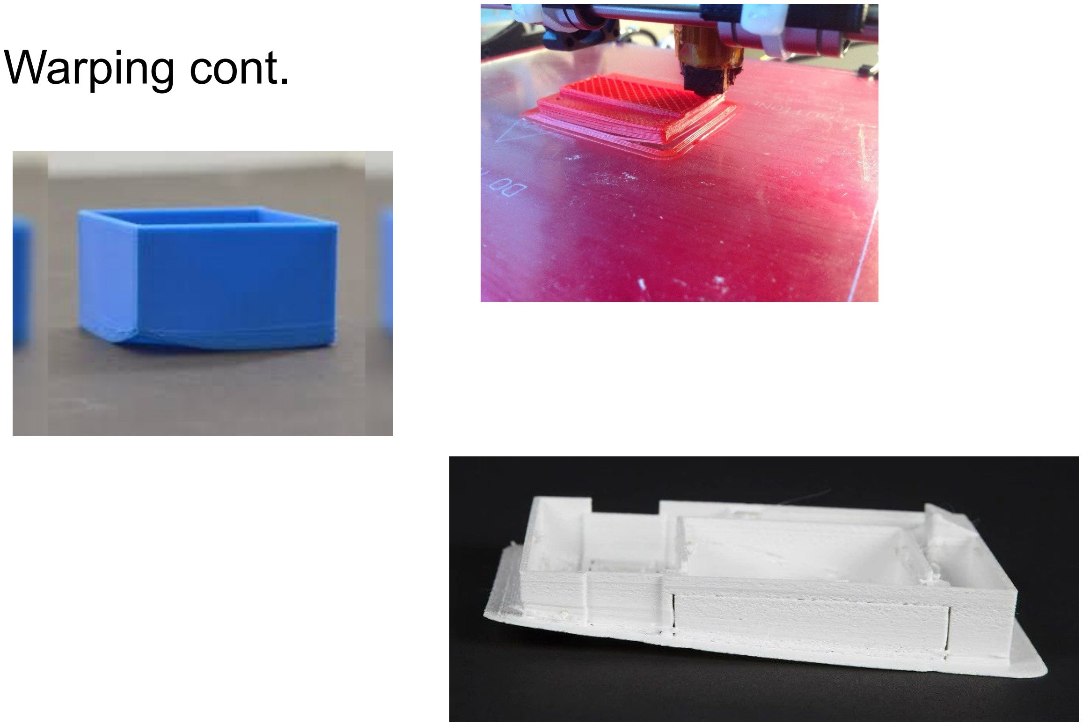
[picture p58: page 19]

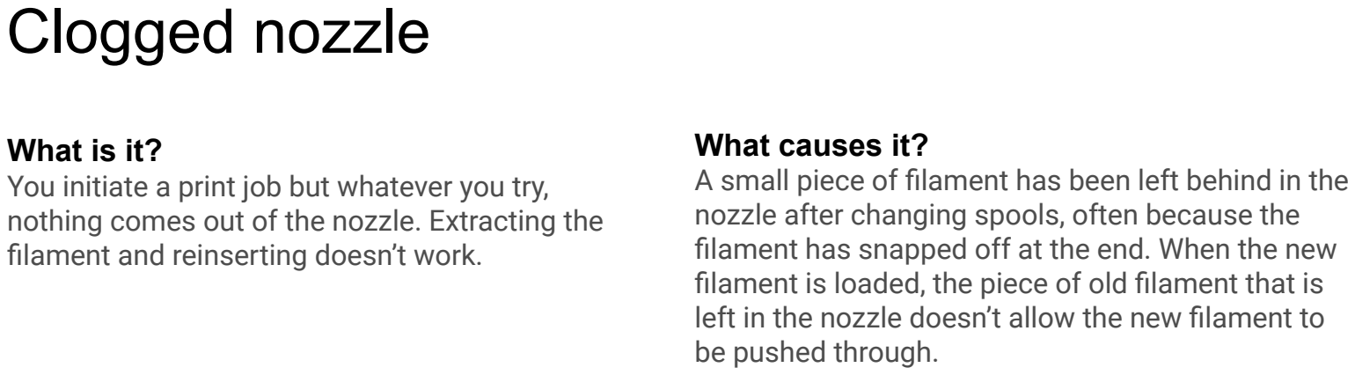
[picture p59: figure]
Clogged nozzle; What is it?; filament and reinserting doesn’t work.; What causes it?; be pushed through.

You initiate a print job but whatever you try,

## nothing comes out of the nozzle. Extracting the

## A small piece of filament has been left behind in the nozzle after changing spools, often because the filament has snapped off at the end. When the new filament is loaded, the piece of old filament that is left in the nozzle doesn’t allow the new filament to

## How do I know?

Filament will not extrude even if it manually fed through the nozzle.

Clogged nozzle cont.

## Solutions: - Unblock with a needle

- If you’re lucky then unblocking can be a quick and easy process. Start by removing the filament. Then using your printer’s control panel select the “heat up nozzle” setting and increase to the melting point of the stuck filament. Once the nozzle reaches the correct temperature, use a small pin to clear the hole (being careful not to burn your fingers)

## - Push the old filament through

- If you find that the nozzle is still blocked then you may be able to push the filament through with another bit of filament. Start by removing the filament as before and then remove the feeder tube from the print head. Heat up the hot end and then using another piece of filament to push this through from the top to try to force the stuck filament in the nozzle out. Usually if the new filament hasn’t succeeded in unblocking then the extra pressure you can exert by hand might just do the job. However don’t push to hard as you’ll risk bending the horizontal printer rods.

## - Disassemble, clear and rebuild the hot end

- In extreme cases when the nozzle remains blocked, you’ll need to do a little surgery and dismantle the hot end. If you’ve never done this before
then it’s a good idea to make notes and take photographs so you know where everything fits when you reassemble. Start by removing the | filament,
then check your printer’s manual to see exactly how to dismantle the hot end.

## - Get aggressive with it

- For nozzles that use PLA, a torch can be used to burn or melt out any excess or clogged filament
- Nozzles that use ABS can be soaked in acetone to melt out excess material

Clogged nozzle cont.

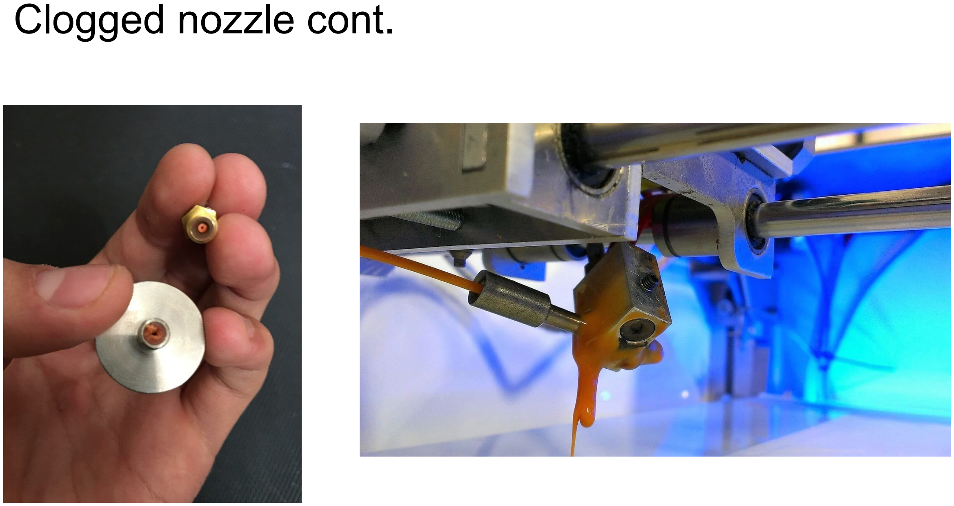
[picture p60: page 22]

# Elephant's foot

## What is it? Elephant's foot is a 3D printing term that refers to the outward bulge of a model's base. Simply put, it is when the print bows or curves out at the bottom

## What causes it? This usually happens when the weight of the model is pressing down on its base before it cools back to solid

## How do I know? Prints will curve out towards the bottom of the print

Elephant's foot cont.

## Solutions

- Another 3D printing troubleshooting tip you can use is to ensure that the base layers get enough coolness so as to be able to support the top structure. You need to ensure that the cooling is just the right amount as too much cooling will cause the base layers to get warped. You might find this part tricky but the best way to go about this 3D printing troubleshooting process is to lower the print platform's temperature by five-degree intervals to about plus or minus twenty degrees of the temperature recommended. If you have your Bottom/Top thickness set to 0.6mm, you can start the fan at a height that's slightly lower than that.

Elephant's foot cont.

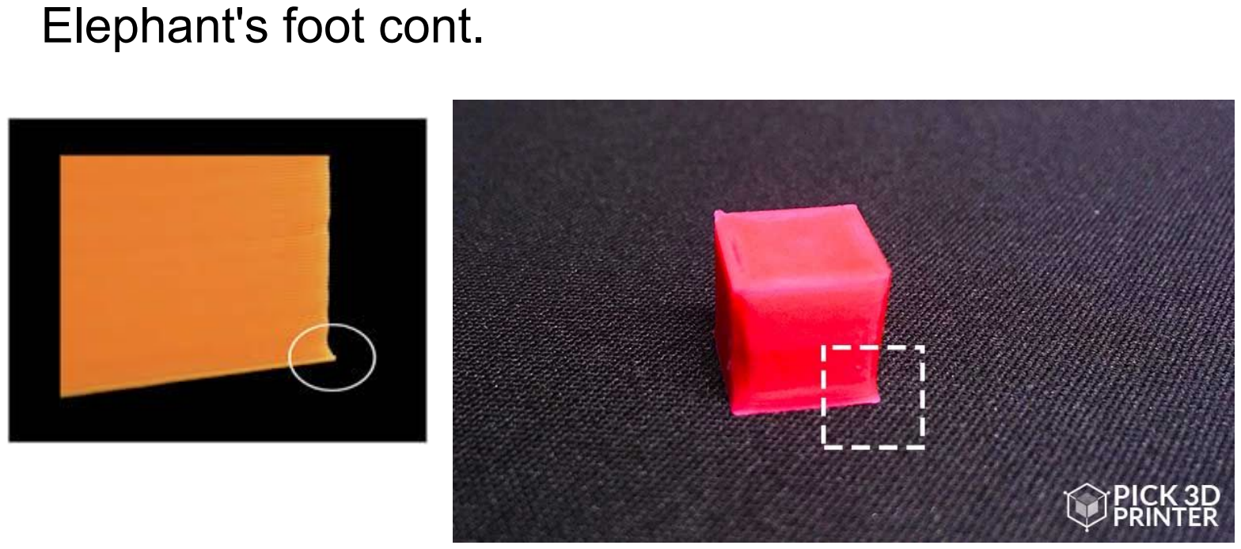
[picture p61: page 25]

# Stringing

## What is it? There are unsightly strings of plastic between parts of the model

## What causes it? When the print head moves over an open area (otherwise known as travel move), some filament has dripped from the nozzle

## How do I know? There are thin spider web looking strands on the print

Stringing cont.

## Solutions: - Enable retraction

- Retraction is an important factor when it comes to quality of finish and can be enabled through most slicing software. Its function is pretty simple and works by retracting the filament back into the nozzle before the head moves. The idea is that it avoids molten filament from trailing behind the head creating thin strings in its wake. Most applications such as Cura offer a one click activation option. This uses a set of default parameters and for the most part is perfectly adequate, but for fine tuning there are customizable options that give greater control. Adjusting the minimum travel of the head before retraction is activated, for example.

## - Minimum travel

- Reducing the minimum travel is usually the quickest fix for stringing if the standard retraction isn’t doing the job. Drop the value in 0.5mm increments until the stringing has stopped.

## - Just cut them off

- This isn’t the most elegant of solutions but simply taking a scalpel to the strings is quite often the quickest and easiest solution.

Stringing cont.

# Bad bowden coupler

## What is it? The coupler/fitting that holds the bowden tube in place is either broken or worn to the point of

failure.

## What causes it?

General use over time, improper use and application, general wear and tear.

## How do I know? The coupler will not be able to hold onto the bowden tube or the tube has been

pushed out of the fitting during a job.

Bad bowden coupler cont.

## Solutions: - Remove and replace

- Remove the coupler on the side that failed. Find/purchase a spare and replace. Install the bowden tube as normal.

Bad bowden coupler cont.

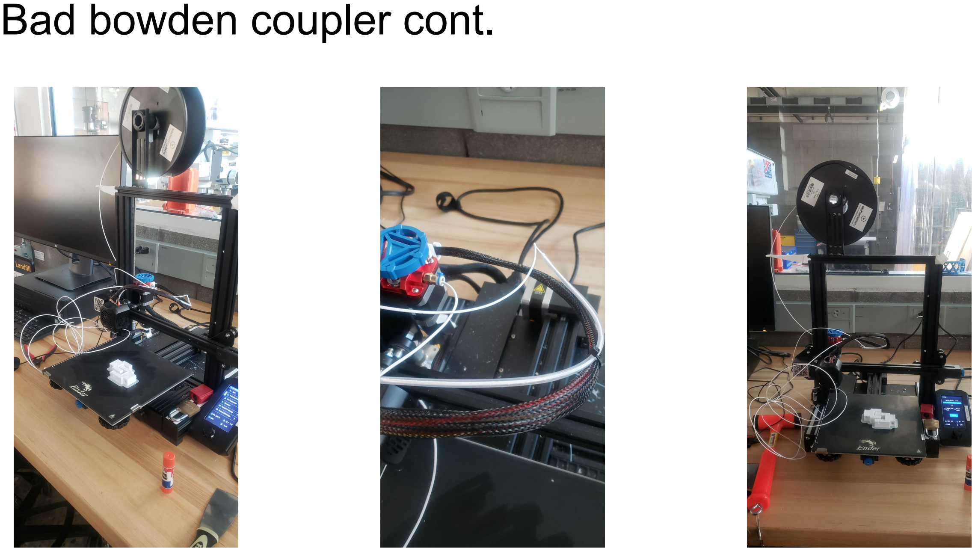
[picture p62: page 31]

# Raft silhouetting (SLA resin)

## What is it?

## “Raft silhouetting” describes a print defect in which the early layers adhere to the build platform, creating a silhouette of the raft or initial layers. After these initial layers that create

the raft silhouette, the remainder of the part does not print.

## What causes it?

## Contamination, dust, or debris on the printer’s optical surfaces can diffuse or weaken laser light, causing a print failure where only the early layers of the print adhere to the

build platform.

## How will I know?

- Only the first few layers adhere to the build platform.
- The rest of the part is missing from the build platform,

## and may be present as cured resin in the tank bottom or

absent entirely.

Raft silhouetting cont.

## Solutions: - Check the resin tank

- Any damage or debris in or on the resin tank can block the laser at that location, preventing the resin directly above it from curing. Inspect the inside and underside of the tank for dirt, dust, and/or fingerprints. The bottom of the tank must be clean for the best print results.
i. Inspect the resin tank for debris with the tank tool.
ii. | Remove any failed prints and cured resin using the tank tool.
iii. | Alternatively, remove any failed prints and cured resin by printing a cleaning mesh.
iv. | Filter the resin to remove any contamination or cured resin.
v. Inspect the flexible film at the bottom of the resin tank for scratches or wear. Excessive wear means the resin tank needs to be replaced. vi. Inspect the underside of the flexible film for dirt, dust, or fingerprints. Clean it with Formlabs recommended steps and supplies.

## - Check the optical window

- Any contamination, dust, or debris on the printer’s optical surfaces can cause the laser light to diffuse or weaken, resulting in a print failure. Contamination is most likely to occur on an exposed optical surface in the printer.
i. With the printer plugged in and powered on, tap the wrench icon on the touchscreen to enter the Settings menu, then tap Maintenance,
| then tap LPU Replacement. The LPU housing moves from its storage position on the right side of the printer into its maintenance position.
ii. | When prompted by the touchscreen, disconnect the power cable before continuing with maintenance.
iii. | Inspect the optical window for contamination.
iv. | Follow the instructions for cleaning the glass optical window.
v. Form 3/Form 3B
vi. | Form 3L/Form 3BL
vii. | If streaks are difficult to remove, contact Formlabs Support or your authorized reseller.

Raft silhouetting cont.

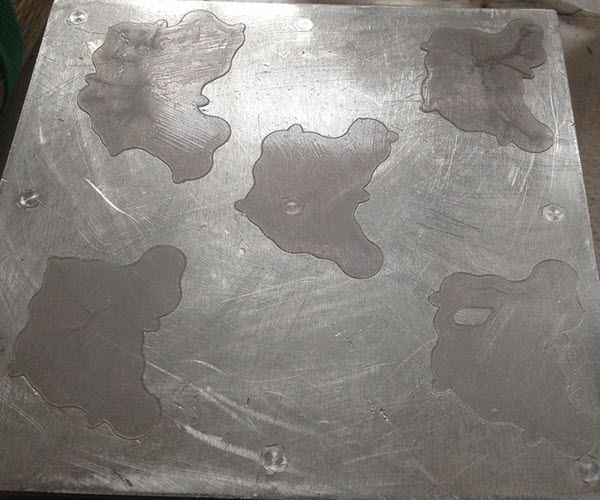
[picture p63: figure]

# No adherence (SLA resin)

## What is it?

## “Non-adherence” describes a print defect in which prints are either partially or completely detached from the build platform. This occurs when the initial layers of a print fail to

adhere to the build platform.

What causes it? Printing without a raft, when the part has no suitable flat surface to grip the build platform. The first layer of the part on the build platform is too small to withstand peel forces. Debris/clouding/damage in the resin tank weakening the printer’s laser. There could be contaminated optical surfaces weakening the printer’s laser. There is excessive space between the build platform and the elastic layer or the flexible film in the resin tank

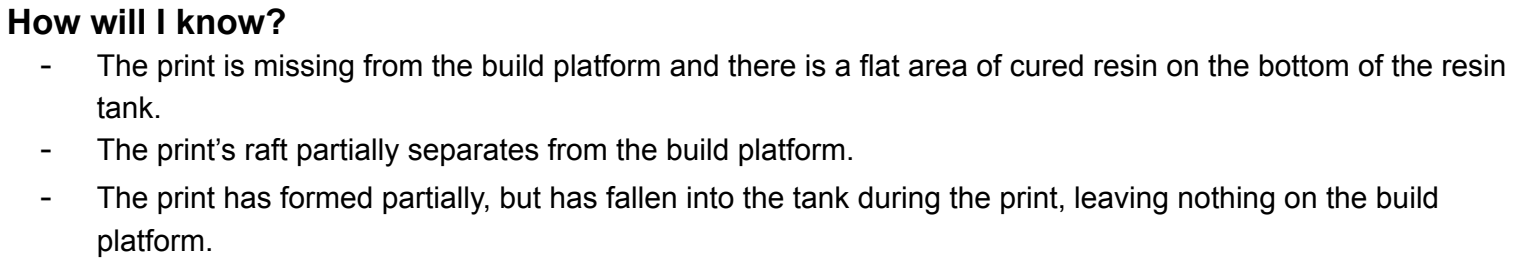
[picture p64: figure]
How will I know?; tank.; platform.

- The print is missing from the build platform and there is a flat area of cured resin on the bottom of the resin
- The print’s raft partially separates from the build platform.
- The print has formed partially, but has fallen into the tank during the print, leaving nothing on the build

No adherence cont.

## Solutions - Check the model’s supports in PreForm

- Printing with a raft helps parts adhere to the build platform. Generate supports in PreForm when setting up your model. Check if the print detached at the point of contact between the model and the supports.

## - Check the model’s orientation in PreForm

- If the surface area of the initial layers is too small, the suction from the peel process may pull the part off the

## build platform. Check the model in PreForm for orientation issues:

1. Orient the model so that the surface area in contact with the build platform is not too small proportional to your part.
- If using a raft, orient your part on a tilt, which is the recommended best practice.
- If printing directly on the build platform, make sure that the part has a large, flat side in direct contact with the platform.

## - Check the resin tank

- Any damage or debris in or on the resin tank can block the laser at that location, preventing the resin directly above it from curing. Inspect the inside and underside of the tank for dirt, dust, and/or fingerprints. The bottom of the tank must be clean for the best print results.

Non adherence cont.

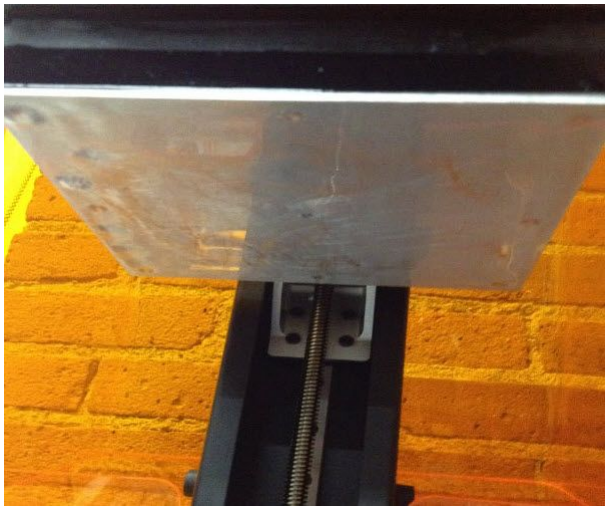
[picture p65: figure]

# Delamination

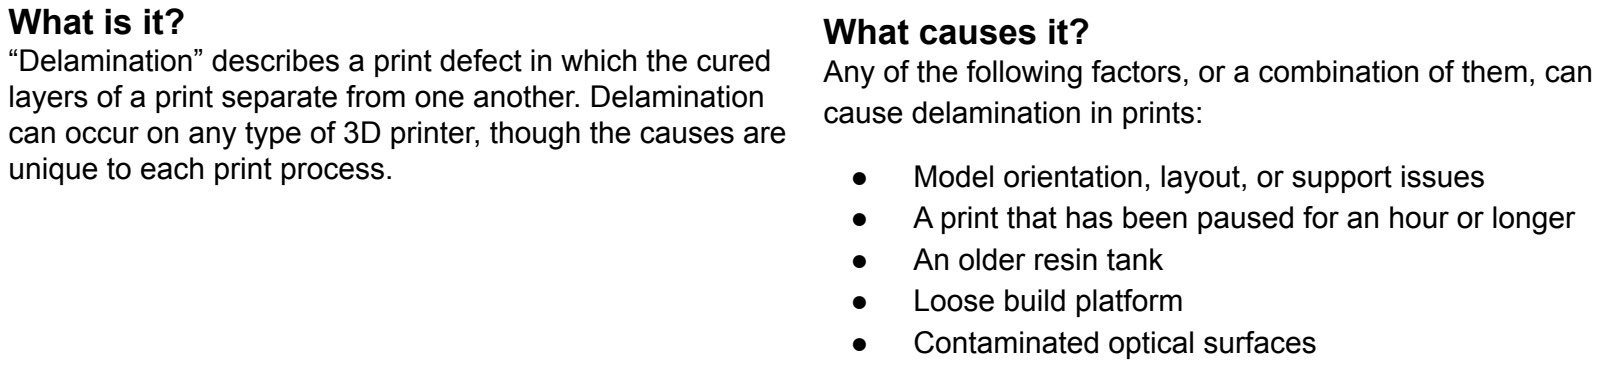
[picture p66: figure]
What is it?; unique to each print process.; What causes it?; cause delamination in prints:; ● An older resin tank ● Loose build platform ● Contaminated optical surfaces

## “Delamination” describes a print defect in which the cured layers of a print separate from one another. Delamination can occur on any type of 3D printer, though the causes are

## Any of the following factors, or a combination of them, can

## - Model orientation, layout, or support issues - A print that has been paused for an hour or longer

## How will I know?

## - Peeling or separation between printed layers - Pieces of cured parts floating in the resin tank

Delamination cont.

## Solutions - Check the model in PreForm

- Lateral forces on the part during the print can disrupt the molecular bonding between layers and separate them. This separation occurs for two reasons:
- The part has a significant change in surface area between subsequent layers. Layers with large surface areas resist print forces better than layers with small surface areas, so a larger layer may separate from a smaller layer during the print. Reorient the part in PreForm to reduce the difference in surface area between neighboring layers.
- Sections of the part are free-hanging or lack adequate supports. In PreForm, look for areas shaded in red, and add supports to these areas.

## - Check for pauses in printing

- Extended pauses during the print can lead to delamination after the print resumes.
- Resolve any errors displayed on the touchscreen that pause the print.
- Enable notifications on Dashboard to receive text or email alerts for print interruptions as soon as they occur.

## - Check the resin tank

- Any damage or debris in or on the resin tank can block the laser at that location, preventing the resin directly above it from curing. Inspect the inside and underside of the tank for dirt, dust, and/or fingerprints. The bottom of the tank must be clean for the best print results.
i. Inspect the resin tank for debris with the tank tool.
ii. | Remove any failed prints and cured resin using the tank tool.
iii. | Alternatively, remove any failed prints and cured resin by printing a cleaning mesh.
iv. | Filter the resin to remove any contamination or cured resin.
v. Inspect the flexible film at the bottom of the resin tank for scratches or wear. Excessive wear means the resin tank needs to be replaced. vi. Inspect the underside of the flexible film for dirt, dust, or fingerprints. Clean it with Formlabs recommended steps and supplies.

## - Check the optical window

- Any contamination, dust, or debris on the printer’s optical surfaces can cause the laser light to diffuse or weaken, resulting in a print failure. Contamination is most likely to occur on an exposed optical surface in the printer.

Delamination cont.

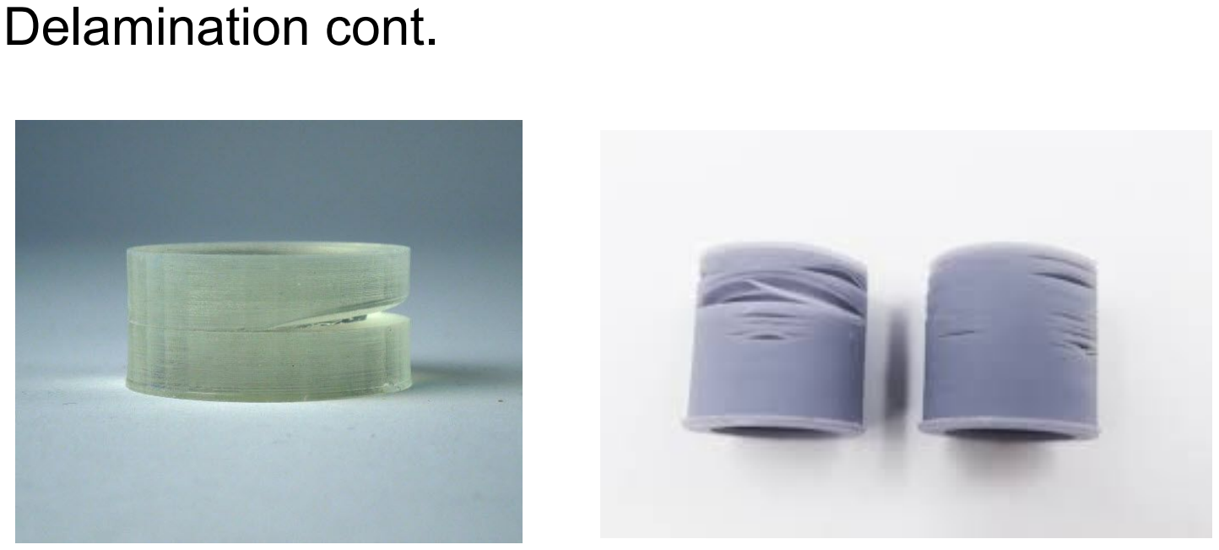
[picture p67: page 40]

# Cupping/blowout

## What is it?

“Cupping” is a concern unique to upside-down stereolithography (SLA) printing. A print failure caused by unresolved cupping is often referred to as a “blowout.” This occurs when a hollow or convex portion of a part acts as a suction cup and traps air while printing. As the build platform pulls away from the tank during the peel process, the empty space within the cup increases. This reduces the air pressure within the cup to create a pressure differential that pushes inward on the surrounding cup walls. If the walls are too thin and unable to withstand the pressure, then they buckle inward to equalize the pressure. Depending on the location of the rupture, the part can potentially continue to print without further errors. The risk of a blowout is dependent on the resin type, size of the cup, shape of the model, and thickness of the cup wall. Small cups, or cups with thicker walls, may print successfully. Formlabs recommends adding a drainage hole and orienting the model in PreForm to minimize cupping.

## What causes it?

## Any of the following factors, or a combination of them, can cause cupping blowout in prints:

## - No drainage holes in hollow or convex parts - Model orientation issues - Model printed without resolving cups highlighted in PreForm

## How will I know?

## - A “hole” in the wall of your part - A large, ragged “rupture” in your part - Poor surface finish on cup surfaces

Cupping/blowout cont.

## Solutions

- Enable Show Cups and inspect the model with the Slicer tool, or add a drainage hole to the cup in your preferred 3D design package before returning the model to PreForm.

Cupping/blowout cont.

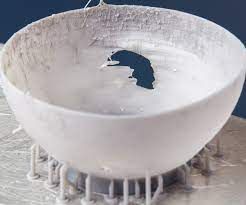
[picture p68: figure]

# Underdeveloped features

## What is it?

An "undeveloped feature" is a print defect in which a void of missing material forms within a print and widens as the print builds away from the build platform. These voids can look like a crater and frequently exhibit sharp edges and rough surfaces. In some cases, it can look like the missing material exploded” outwards from the build platform. This type of defect is a print failure unique to stereolithography (SLA). If a piece of the print sticks to the bottom of the resin tank, that piece partially blocks the laser from reaching the next layer of the print. The piece stuck to the tank expands with each additional cured layer and prevents other features from forming.

## What causes it?

## Any of the following factors, or a combination of them, can cause prints to have undeveloped features:

## - Debris or damage in resin tanks - Clouding in Form 2 standard resin tanks - Model orientation, layout, or support issues - Contaminated optical surfaces

## How will I know?

- A void within a print that expands outwards from the earliest layer to the most recent layer,

## usually with sharp edges and rough surfaces like a crater - A layer of cured resin on the bottom of the resin tank

Underdeveloped features cont.

## Solutions - Check the model in PreForm

- Inspect the printed part to determine where the undeveloped feature started. In PreForm, look for the area on the part where the outward-expanding explosion is closest to the build platform.
- Examine individual layers of the model with the vertical Slicer tool on the right side of PreForm. Pay close attention to the following areas as the possible origin for the undeveloped feature:
- Look for any areas on the model highlighted in red. These highlighted areas indicate printability concerns and may need additional support.
- Even if there is no red shading, consider adding extra supports to any areas that failed during printing.
- In particular, look for local minima and islands that need additional support.

## - Check the resin tank

- Any damage or debris in or on the resin tank can block the laser at that location, preventing the resin directly above it from curing. Inspect the inside and underside of the tank for dirt, dust, and/or fingerprints. The bottom of the tank must be clean for the best print results.
- Inspect the resin tank for debris with the tank tool.
- Remove any failed prints and cured resin using the tank tool.
- Alternatively, remove any failed prints and cured resin by printing a cleaning mesh.
- Filter the resin to remove any contamination or cured resin.
- Inspect the flexible film at the bottom of the resin tank for scratches or wear. Excessive wear means the resin tank needs to be replaced.
- Inspect the underside of the flexible film for dirt, dust, or fingerprints. Clean it with Formlabs recommended steps and supplies.

## - Check the optical window

- Any contamination, dust, or debris on the printer’s optical surfaces can cause the laser light to diffuse or weaken, resulting in a print failure. Contamination is most likely to occur on an exposed optical surface in the printer.
- With the printer plugged in and powered on, tap the wrench icon on the touchscreen to enter the Settings menu, then tap Maintenance, then tap LPU Replacement. The LPU housing moves from its storage position on the right side of the printer into its maintenance position.
- When prompted by the touchscreen, disconnect the power cable before continuing with maintenance.
- Inspect the optical window for contamination.
- Follow the instructions for cleaning the glass optical window.
- If streaks are difficult to remove, contact Formlabs Support or your authorized reseller.

Underdeveloped features cont.

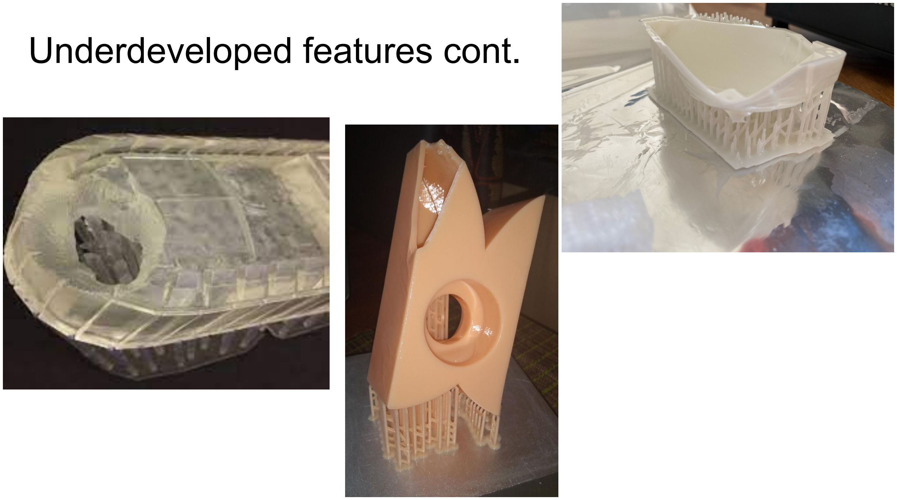
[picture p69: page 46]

# Pinholes or cuts

## What are they?

A “pinhole” or “cut” describes a print defect in which a small region of the part does not form. This void can take the form of a small hole, a tunnel that runs through the part, or a slit that cuts through the part. If other sections of the part would have been supported directly by the missing material, those sections may also fail to cure to

the part.

## What causes them?

## - Debris or scratches on the bottom surface of the resin tank - Debris or scratches on the optical window or another optical surface

## If, while curing a layer, the laser is blocked before it reaches the resin, that portion of the part will not form properly. If the obstruction is on a stationary surface, a hole may develop directly above that point. If the blockage is on

a moving surface, a linear cut may develop instead, following the path of the blockage.

## How will I know?

- A void that passes through the entire print, including the raft (if one is used). The void may take the form of a small hole in one portion of the part or a linear slit that extends across the part.

## - A hole or cut may lead to one or more undeveloped features,depending on the

geometry and orientation of the part.

Pinholes or cuts cont.

## Solutions - Check the resin tank

- Any damage or debris in or on the resin tank can block the laser at that location, preventing the resin directly above it from curing. Inspect the inside and underside of the tank for dirt, dust, and/or fingerprints. The bottom of the tank must be clean for the best print results. Any debris, clouding, or damage to the resin tank can diffuse the laser light and limit the printer’s ability to fully cure the resin.
- Inspect the resin tank for debris with the tank tool.
- Remove any failed prints and cured resin using the tank tool.
- Alternatively, remove any failed prints and cured resin by printing a cleaning mesh.
- Filter the resin to remove any contamination or cured resin.
- Inspect the flexible film at the bottom of the resin tank for scratches or wear. Excessive wear means the resin tank needs to be replaced.
- Inspect the underside of the flexible film for dirt, dust, or fingerprints. Clean it with Formlabs recommended steps and supplies.

## - Check the optical window

- Any contamination, debris, or scratches on an optical surface can also block the laser at that location, preventing the resin directly above it from curing. Contamination is most likely to occur on an exposed optical surface in the printer. The optical surface most likely to be contaminated is the glass optical window, which sits atop the Light Processing Unit (LPU).
1. With the printer plugged in and powered on, tap the wrench icon on the touchscreen to enter the Settings menu, then tap Maintenance, then tap LPU Replacement. The LPU housing moves from its storage position on the right side of the printer into its maintenance position.
2. When prompted by the touchscreen, disconnect the power cable before continuing with maintenance.
3. Inspect the optical window for contamination.
4. Follow the instructions for cleaning the glass optical window.
5. If streaks are difficult to remove, contact Formlabs Support or your

Pinholes or cuts cont.

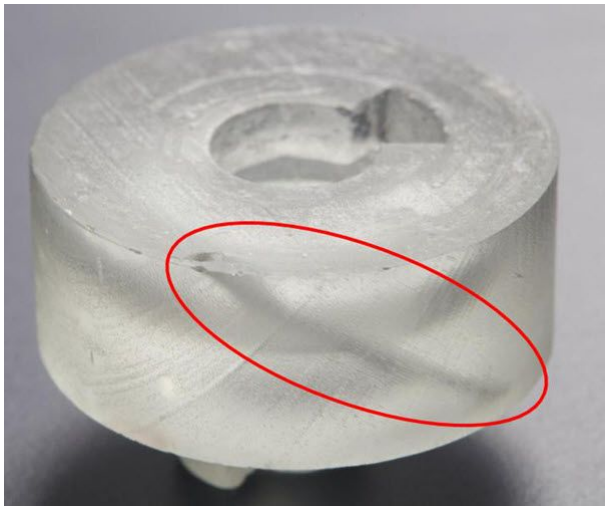
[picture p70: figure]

# Ragging

## What is it?

## “Ragging” describes a print defect in which cured or partially cured resin forms thin, shelf-like structures that hang horizontally from a print. These structures, also called

“flaps,” can detach from the part during printing.

## Once these flaps are floating in the resin tank, they can block the laser’s path and cause print failures in subsequent layers. Ragging occurs when diffused laser light spreads the cure area beyond the appropriate limits for each layer

outline.

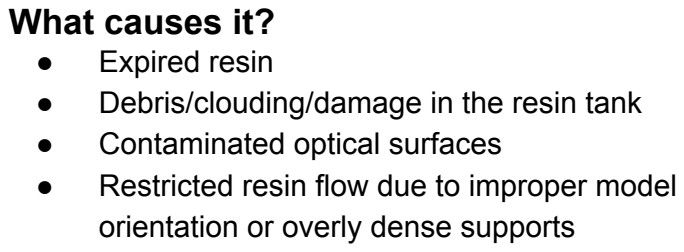
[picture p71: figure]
What causes it? ● Expired resin; ● Contaminated optical surfaces; orientation or overly dense supports

## - Debris/clouding/damage in the resin tank

## - Restricted resin flow due to improper model

## How will I know?

## - Flaps of cured or partially cured resin on the print that degrade the overall cosmetic aspects of the print

- Thin flakes of cured or partially cured resin from the print floating in the resin tank,

## which may or may not cause a print failure

Ragging cont.

## Solutions - Check the resin’s expiration date

- Parts printed with expired resin may have poor surface finish and exhibit rashing and ragging. Formlabs resins last for 12 to 24 months in the resin cartridge, depending on the resin type. Learn more about resin lifetime and storage to determine if your resin has expired.

## - Check the resin tank

- Any damage or debris in or on the resin tank can block the laser at that location, preventing the resin directly above it from curing. Inspect the inside and underside of the tank for dirt, dust, and/or fingerprints. The bottom of the tank must be clean for the best print results.
- Inspect the resin tank for debris with the tank tool.
- Remove any failed prints and cured resin using the tank tool.
- Alternatively, remove any failed prints and cured resin by printing a cleaning mesh.
- Filter the resin to remove any contamination or cured resin.
- Inspect the flexible film at the bottom of the resin tank for scratches or wear. Excessive wear means the resin tank needs to be replaced.
- Inspect the underside of the flexible film for dirt, dust, or fingerprints. Clean it with Formlabs recommended steps and supplies

## - Check the optical window

- Any contamination, dust, or debris on the printer’s optical surfaces can cause the laser light to diffuse or weaken, resulting in a print failure. Contamination is most likely to occur on an exposed optical surface in the printer. The optical surface most likely to be contaminated is the glass optical window, which sits atop the Light Processing Unit (LPU).
1. With the printer plugged in and powered on, tap the wrench icon on the touchscreen to enter the Settings menu, then tap Maintenance, then tap LPU Replacement. The LPU housing moves from its storage position on the right side of the printer into its maintenance position.
2. When prompted by the touchscreen, disconnect the power cable before continuing with maintenance.
3. Inspect the optical window for contamination.
4. Follow the instructions for cleaning the glass optical window.

## - Check for restricted resin flow

Ragging cont.

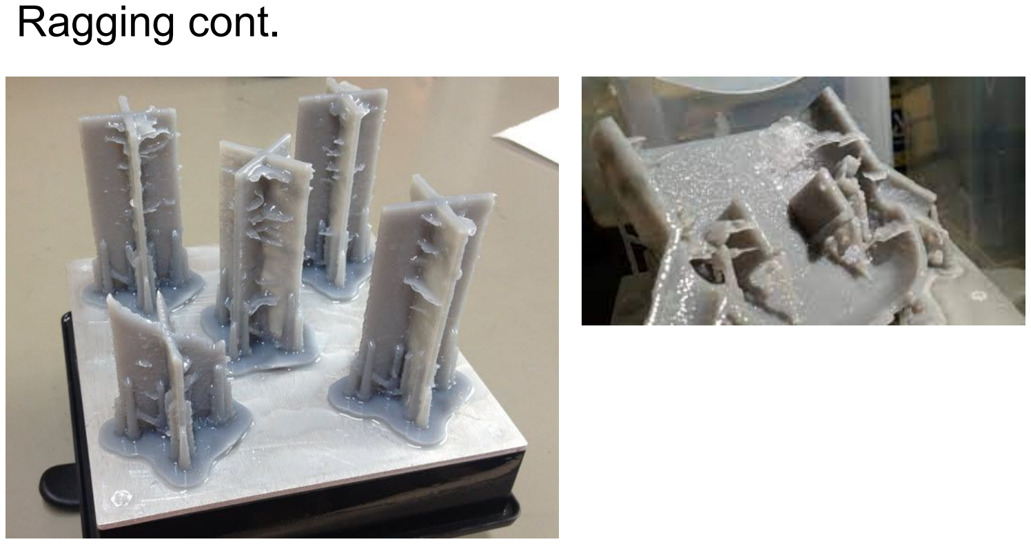
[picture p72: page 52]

# Rashing

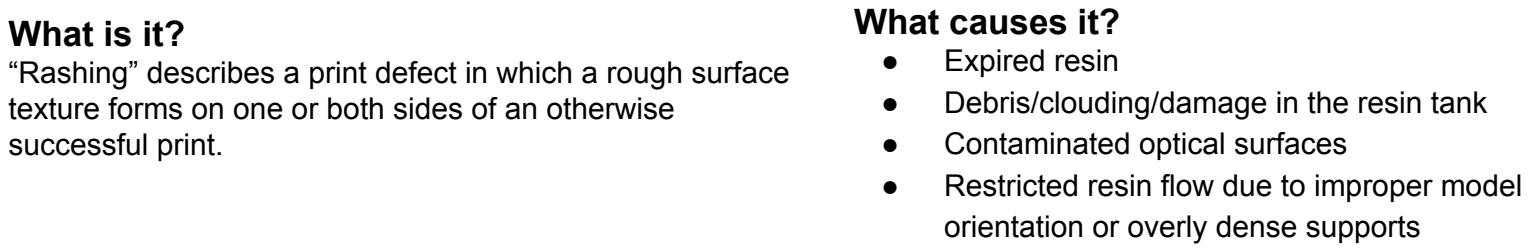
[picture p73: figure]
What is it?; successful print.; What causes it? ● Expired resin; ● Contaminated optical surfaces; orientation or overly dense supports

## “Rashing” describes a print defect in which a rough surface texture forms on one or both sides of an otherwise

## - Debris/clouding/damage in the resin tank

## - Restricted resin flow due to improper model

## How will I know?

For prints created on Formlabs printers, rashing produces an uneven or bumpy surface finish on one or both sides of a part.

Rashing cont.

## Solutions - Check the resin’s expiration date

- Parts printed with expired resin may have poor surface finish and exhibit ragging and rashing. Formlabs resins last for 12 to 24 months in the resin cartridge, depending on the resin type. Learn more about resin lifetime and storage to determine if your resin has expired.

## - Check the resin tank

- Any damage or debris in or on the resin tank can block the laser at that location, preventing the resin directly above it from curing. Inspect the inside and underside of the tank for dirt, dust, and/or fingerprints. The bottom of the tank must be clean for the best print results.
- Inspect the resin tank for debris with the tank tool.
- Remove any failed prints and cured resin using the tank tool.
- Alternatively, remove any failed prints and cured resin by printing a cleaning mesh.
- Filter the resin to remove any contamination or cured resin.
- Inspect the flexible film at the bottom of the resin tank for scratches or wear. Excessive wear means the

## resin tank - Check the optical window

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

## - Check for restricted resin flow

Rashing cont.

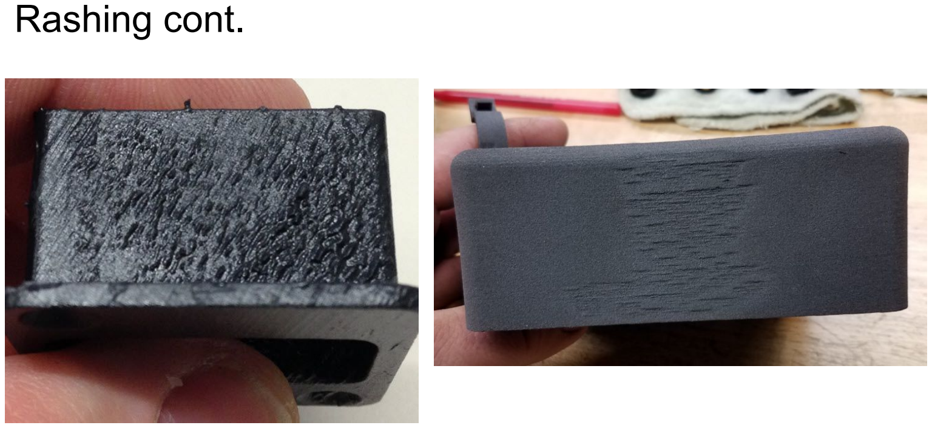
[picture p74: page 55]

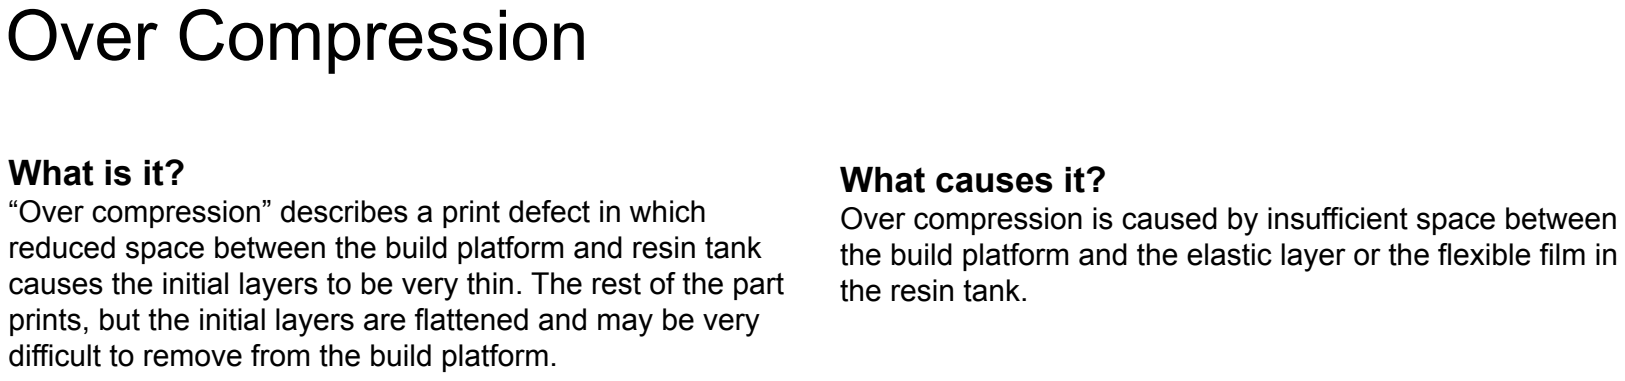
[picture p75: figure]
Over Compression; What is it?; What causes it?; the resin tank.

## “Over compression” describes a print defect in which reduced space between the build platform and resin tank causes the initial layers to be very thin. The rest of the part prints, but the initial layers are flattened and may be very

difficult to remove from the build platform.

## Over compression is caused by insufficient space between the build platform and the elastic layer or the flexible film in

## How will I know?

- The raft is compressed and thinner than expected.
- Parts are especially difficult to remove.
- The raft is completely flat and supports are significantly shorter than expected.

Over compression cont.

## Solutions - Contact support

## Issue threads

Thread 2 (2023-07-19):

Gear Ratio for Pololu 37D gearmotors

pkr97, 2023-07-19:
Hi, What is the gear ratio and power rating of the motor used to build the robot?

Thanks...

halldm3663, 2024-05-21:
did anyone ever get back to you on this?

michiganrobotics, 2024-05-21:
Hello -- apologies for the delay.

The gear ratio of the motor is 70:1 and other motor specification can be found here: https://www.pololu.com/product/4754/resources

Closed 2024-05-22.

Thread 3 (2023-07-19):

U-M Robotics Pico Board: Open Source?

pkr97, 2023-07-19:
Hi, in Lab-8 I see that U-M Robotics Pico Board is used to control the wheels and an additional Raspberry Pi for High-level control.
https://github.com/michiganrobotics/rob311/blob/main/Labs/Lab%2008%20-%20Reading%20and%20plotting%20data/ROB%20311%20-%20Lab%208%20-%20Flashing%2C%20reading%2C%20and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

I was wondering if the U-M Robotics Pico Board is available outside for buying or if the design is open.

If not, can we just have a connection diagram for Pico and DRV8874?

Thanks...

michiganrobotics, 2024-05-21:
Hello -- please find the Pico board specifics here:
https://github.com/mbot-project/mbot_hardware/tree/main/mbot_pico_plus

Closed 2024-05-22.

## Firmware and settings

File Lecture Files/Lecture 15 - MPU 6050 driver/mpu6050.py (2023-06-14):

#!/usr/bin/python

# Python Standard Library Imports
from time import sleep
import math
from math import atan, atan2, sqrt 
import traceback

# External Imports
pass

# Custom Imports
from pycomms import PyComms

class MPU6050:
    # Register map based on Jeff Rowberg <jeff@rowberg.net> source code at
    # https://github.com/jrowberg/i2cdevlib/blob/master/Arduino/MPU6050/MPU6050.h
    CONST_G                       = 9.81 # gravitational const
    
    MPU6050_ADDRESS_AD0_LOW       = 0x68 # address pin low (GND), default for InvenSense evaluation board
    MPU6050_ADDRESS_AD0_HIGH      = 0x69 # address pin high (VCC)
    MPU6050_DEFAULT_ADDRESS       = MPU6050_ADDRESS_AD0_LOW

    MPU6050_RA_XG_OFFS_TC         = 0x00 # [7] PWR_MODE, [6:1] XG_OFFS_TC, [0] OTP_BNK_VLD
    MPU6050_RA_YG_OFFS_TC         = 0x01 # [7] PWR_MODE, [6:1] YG_OFFS_TC, [0] OTP_BNK_VLD
    MPU6050_RA_ZG_OFFS_TC         = 0x02 # [7] PWR_MODE, [6:1] ZG_OFFS_TC, [0] OTP_BNK_VLD
    MPU6050_RA_X_FINE_GAIN        = 0x03 # [7:0] X_FINE_GAIN
    MPU6050_RA_Y_FINE_GAIN        = 0x04 # [7:0] Y_FINE_GAIN
    MPU6050_RA_Z_FINE_GAIN        = 0x05 # [7:0] Z_FINE_GAIN
    MPU6050_RA_XA_OFFS_H          = 0x06 # [15:0] XA_OFFS
    MPU6050_RA_XA_OFFS_L_TC       = 0x07
    MPU6050_RA_YA_OFFS_H          = 0x08 # [15:0] YA_OFFS
    MPU6050_RA_YA_OFFS_L_TC       = 0x09
    MPU6050_RA_ZA_OFFS_H          = 0x0A # [15:0] ZA_OFFS
    MPU6050_RA_ZA_OFFS_L_TC       = 0x0B
    MPU6050_RA_XG_OFFS_USRH       = 0x13 # [15:0] XG_OFFS_USR
    MPU6050_RA_XG_OFFS_USRL       = 0x14
    MPU6050_RA_YG_OFFS_USRH       = 0x15 # [15:0] YG_OFFS_USR
    MPU6050_RA_YG_OFFS_USRL       = 0x16
    MPU6050_RA_ZG_OFFS_USRH       = 0x17 # [15:0] ZG_OFFS_USR
    MPU6050_RA_ZG_OFFS_USRL       = 0x18
    MPU6050_RA_SMPLRT_DIV         = 0x19
    MPU6050_RA_CONFIG             = 0x1A
    MPU6050_RA_GYRO_CONFIG        = 0x1B
    MPU6050_RA_ACCEL_CONFIG       = 0x1C
    MPU6050_RA_FF_THR             = 0x1D
    MPU6050_RA_FF_DUR             = 0x1E
    MPU6050_RA_MOT_THR            = 0x1F
    MPU6050_RA_MOT_DUR            = 0x20
    MPU6050_RA_ZRMOT_THR          = 0x21
    MPU6050_RA_ZRMOT_DUR          = 0x22
    MPU6050_RA_FIFO_EN            = 0x23
    MPU6050_RA_I2C_MST_CTRL       = 0x24
    MPU6050_RA_I2C_SLV0_ADDR      = 0x25
    MPU6050_RA_I2C_SLV0_REG       = 0x26
    MPU6050_RA_I2C_SLV0_CTRL      = 0x27
    MPU6050_RA_I2C_SLV1_ADDR      = 0x28
    MPU6050_RA_I2C_SLV1_REG       = 0x29
    MPU6050_RA_I2C_SLV1_CTRL      = 0x2A
    MPU6050_RA_I2C_SLV2_ADDR      = 0x2B
    MPU6050_RA_I2C_SLV2_REG       = 0x2C
    MPU6050_RA_I2C_SLV2_CTRL      = 0x2D
    MPU6050_RA_I2C_SLV3_ADDR      = 0x2E
    MPU6050_RA_I2C_SLV3_REG       = 0x2F
    MPU6050_RA_I2C_SLV3_CTRL      = 0x30
    MPU6050_RA_I2C_SLV4_ADDR      = 0x31
    MPU6050_RA_I2C_SLV4_REG       = 0x32
    MPU6050_RA_I2C_SLV4_DO        = 0x33
    MPU6050_RA_I2C_SLV4_CTRL      = 0x34
    MPU6050_RA_I2C_SLV4_DI        = 0x35
    MPU6050_RA_I2C_MST_STATUS     = 0x36
    MPU6050_RA_INT_PIN_CFG        = 0x37
    MPU6050_RA_INT_ENABLE         = 0x38
    MPU6050_RA_DMP_INT_STATUS     = 0x39
    MPU6050_RA_INT_STATUS         = 0x3A
    MPU6050_RA_ACCEL_XOUT_H       = 0x3B
    MPU6050_RA_ACCEL_XOUT_L       = 0x3C
    MPU6050_RA_ACCEL_YOUT_H       = 0x3D
    MPU6050_RA_ACCEL_YOUT_L       = 0x3E
    MPU6050_RA_ACCEL_ZOUT_H       = 0x3F
    MPU6050_RA_ACCEL_ZOUT_L       = 0x40
    MPU6050_RA_TEMP_OUT_H         = 0x41
    MPU6050_RA_TEMP_OUT_L         = 0x42
    MPU6050_RA_GYRO_XOUT_H        = 0x43
    MPU6050_RA_GYRO_XOUT_L        = 0x44
    MPU6050_RA_GYRO_YOUT_H        = 0x45
    MPU6050_RA_GYRO_YOUT_L        = 0x46
    MPU6050_RA_GYRO_ZOUT_H        = 0x47
    MPU6050_RA_GYRO_ZOUT_L        = 0x48
    MPU6050_RA_EXT_SENS_DATA_00   = 0x49
    MPU6050_RA_EXT_SENS_DATA_01   = 0x4A
    MPU6050_RA_EXT_SENS_DATA_02   = 0x4B
    MPU6050_RA_EXT_SENS_DATA_03   = 0x4C
    MPU6050_RA_EXT_SENS_DATA_04   = 0x4D
    MPU6050_RA_EXT_SENS_DATA_05   = 0x4E
    MPU6050_RA_EXT_SENS_DATA_06   = 0x4F
    MPU6050_RA_EXT_SENS_DATA_07   = 0x50
    MPU6050_RA_EXT_SENS_DATA_08   = 0x51
    MPU6050_RA_EXT_SENS_DATA_09   = 0x52
    MPU6050_RA_EXT_SENS_DATA_10   = 0x53
    MPU6050_RA_EXT_SENS_DATA_11   = 0x54
    MPU6050_RA_EXT_SENS_DATA_12   = 0x55
    MPU6050_RA_EXT_SENS_DATA_13   = 0x56
    MPU6050_RA_EXT_SENS_DATA_14   = 0x57
    MPU6050_RA_EXT_SENS_DATA_15   = 0x58
    MPU6050_RA_EXT_SENS_DATA_16   = 0x59
    MPU6050_RA_EXT_SENS_DATA_17   = 0x5A
    MPU6050_RA_EXT_SENS_DATA_18   = 0x5B
    MPU6050_RA_EXT_SENS_DATA_19   = 0x5C
    MPU6050_RA_EXT_SENS_DATA_20   = 0x5D
    MPU6050_RA_EXT_SENS_DATA_21   = 0x5E
    MPU6050_RA_EXT_SENS_DATA_22   = 0x5F
    MPU6050_RA_EXT_SENS_DATA_23   = 0x60
    MPU6050_RA_MOT_DETECT_STATUS  = 0x61
    MPU6050_RA_I2C_SLV0_DO        = 0x63
    MPU6050_RA_I2C_SLV1_DO        = 0x64
    MPU6050_RA_I2C_SLV2_DO        = 0x65
    MPU6050_RA_I2C_SLV3_DO        = 0x66
    MPU6050_RA_I2C_MST_DELAY_CTRL = 0x67
    MPU6050_RA_SIGNAL_PATH_RESET  = 0x68
    MPU6050_RA_MOT_DETECT_CTRL    = 0x69
    MPU6050_RA_USER_CTRL          = 0x6A
    MPU6050_RA_PWR_MGMT_1         = 0x6B
    MPU6050_RA_PWR_MGMT_2         = 0x6C
    MPU6050_RA_BANK_SEL           = 0x6D
    MPU6050_RA_MEM_START_ADDR     = 0x6E
    MPU6050_RA_MEM_R_W            = 0x6F
    MPU6050_RA_DMP_CFG_1          = 0x70
    MPU6050_RA_DMP_CFG_2          = 0x71
    MPU6050_RA_FIFO_COUNTH        = 0x72
    MPU6050_RA_FIFO_COUNTL        = 0x73
    MPU6050_RA_FIFO_R_W           = 0x74
    MPU6050_RA_WHO_AM_I           = 0x75  

    MPU6050_TC_PWR_MODE_BIT    = 7
    MPU6050_TC_OFFSET_BIT      = 6
    MPU6050_TC_OFFSET_LENGTH   = 6
    MPU6050_TC_OTP_BNK_VLD_BIT = 0

    MPU6050_VDDIO_LEVEL_VLOGIC  = 0
    MPU6050_VDDIO_LEVEL_VDD     = 1    

    MPU6050_CFG_EXT_SYNC_SET_BIT    = 5
    MPU6050_CFG_EXT_SYNC_SET_LENGTH = 3
    MPU6050_CFG_DLPF_CFG_BIT    = 2
    MPU6050_CFG_DLPF_CFG_LENGTH = 3

    MPU6050_EXT_SYNC_DISABLED      = 0x0
    MPU6050_EXT_SYNC_TEMP_OUT_L    = 0x1
    MPU6050_EXT_SYNC_GYRO_XOUT_L   = 0x2
    MPU6050_EXT_SYNC_GYRO_YOUT_L   = 0x3
    MPU6050_EXT_SYNC_GYRO_ZOUT_L   = 0x4
    MPU6050_EXT_SYNC_ACCEL_XOUT_L  = 0x5
    MPU6050_EXT_SYNC_ACCEL_YOUT_L  = 0x6
    MPU6050_EXT_SYNC_ACCEL_ZOUT_L  = 0x7

    MPU6050_DLPF_BW_256        = 0x00
    MPU6050_DLPF_BW_188        = 0x01
    MPU6050_DLPF_BW_98         = 0x02
    MPU6050_DLPF_BW_42         = 0x03
    MPU6050_DLPF_BW_20         = 0x04
    MPU6050_DLPF_BW_10         = 0x05
    MPU6050_DLPF_BW_5          = 0x06

    MPU6050_GCONFIG_FS_SEL_BIT     = 4
    MPU6050_GCONFIG_FS_SEL_LENGTH  = 2

    MPU6050_GYRO_FS_250        = 0x00
    MPU6050_GYRO_FS_500        = 0x01
    MPU6050_GYRO_FS_1000       = 0x02
    MPU6050_GYRO_FS_2000       = 0x03
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

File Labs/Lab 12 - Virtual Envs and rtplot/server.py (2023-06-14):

# Import communication
import zmq

# Import plotting
from pyqtgraph.Qt import QtGui, QtCore, QtWidgets
import pyqtgraph as pg

# Common imports 
import numpy as np
import pandas as pd 
import os
import time

# Get timer to calculate fps
from time import perf_counter

# Import argparse to handle different configurations
# of the plotter
import argparse

#Import date_time to save timestamps
import datetime

############################
# Command Line Arguments #
###########################

# Create command line arguments
parser = argparse.ArgumentParser()

#Add argument to enable bigger fonts
parser.add_argument('-p','--pi_ip', help="The IP address for the pi, if you don't add this it will default to 10.0.0.200", 
                    action='store', type=str)
parser.add_argument("-b","--bigscreen", help="Increase fonts to print in the big screen",
                    action="store_true")
parser.add_argument('-l','--local', help="Run local plotting server", 
                    action="store_true")
parser.add_argument('-s','--static_ip', help="Use this to connec the pi to your computer when it has a konwn fixed IP", 
                    action="store_true")
parser.add_argument('-c','--column', help="Create new plots in separate columns",
                    action="store_false")
parser.add_argument("-d","--debug", help="Add debug text output",action="store_true")
args = parser.parse_args()

# If big screen mode is on, set font sizes big
if args.bigscreen:
    axis_label_style = {'font-size':'20pt'}
    title_style = {'size':'25pt'}
    #Accepts parameters into LegendItem constructor
    legend_style = {'labelTextSize':'14pt'}
    tick_size = 25
    
# Else set to normal size
else:
    axis_label_style = {'font-size':'10pt'}
    title_style = {'size':'14pt'}
    legend_style = {'labelTextSize':'8pt'}
    tick_size = 12

#Get flag for local plotting
fixed_address = args.local or args.static_ip

# Define if a new subplot is placed in a 
# new row or columns
NEW_SUBPLOT_IN_ROW = args.column

#Define if debug text output is set on
DEBUG_TEXT_ENABLED = args.debug

###################
# ZMQ Networking #
##################

# Create connection layer
context = zmq.Context()

# Using the pub - sub paradigm
socket = context.socket(zmq.SUB)

#Current default is to connect to the neurobionics pi hotspot
# since that is the current use case
if args.pi_ip is not None:
    #Connect to the supplied IP address
    connect_string = f"tcp://{args.pi_ip}:5555"
    socket.connect(connect_string)
    print(f'Connected to {connect_string}')

#Elif default to a known address
elif not fixed_address:
    #Connect to neurobionics pi - default behaviour for now
    connect_string = "tcp://10.0.0.200:5555"

    socket.connect(connect_string)
    print(f'Connected to {connect_string}')
   
#If we have a fixed address, then the subscriber can reach us
# good for local plots or fixed ip address
else:
    #Bind so that you can get more
    socket.bind("tcp://*:5555")
    print("Bounded every ip address on port :5555")

#Initialize subscriber
socket.setsockopt_string(zmq.SUBSCRIBE, "")


###############################
# Local Storage Configuration #
###############################

# Width of the window displaying the curve
NUM_DATAPOINTS_IN_PLOT = 500

#Num of entry buffers
MAX_LOCAL_STORAGE = 100000

#Initial number of traces
INITIAL_NUM_TRACES = 50

#Storage buffer - This will take around 3.73 GB of ram
# Should last for 27 hours running at 100 Hz
local_storage_buffer = np.zeros((INITIAL_NUM_TRACES,MAX_LOCAL_STORAGE))

#Create an index to keep track where we are in the local storage buffer
li = NUM_DATAPOINTS_IN_PLOT

#Set how many traces we have 
local_storage_buffer_num_trace = 1

#To use the local storage buffer as the plotter array
# we need to keep track of the bounds
buffer_bounds = np.array([0,NUM_DATAPOINTS_IN_PLOT])

#Configure save path
PLOT_SAVE_PATH = './'

#We are going to use the traces per plot do add info to saved plots
# since this is set below, initialize to none
traces_per_plot = None
trace_info = None

#Create button callback method
def save_current_plot():

    #Set which trace goes in which plot on the last element of the column
    num_subplots = 0
    trace_names = []
    for i,(trace_name,subplot_index) in enumerate(trace_info):
        # Add subplot index to last column
        local_storage_buffer[i,li] = subplot_index
        # Get the number of subplots
        num_subplots = max(subplot_index,num_subplots)
        # Add trace name
        trace_names.append(trace_name)
    
    #Assign a new subplot for time
    num_traces = len(trace_info)
    trace_names.append("Time(s)")
    local_storage_buffer[num_traces,li] = num_subplots+1

    #Set the plot name as the current time
    plot_name = datetime.datetime.now()
    total_name = os.path.join(PLOT_SAVE_PATH, str(plot_name).replace(' ','_')+'.parquet')
    
    #Create the dataframe object so that we can add ifnro about the subplot names
    df = pd.DataFrame(local_storage_buffer[:local_storage_buffer_num_trace,NUM_DATAPOINTS_IN_PLOT:li+1].T,
                      columns=trace_names)
    df.to_parquet(total_name)

    #Output text confirming we saved
    print(f"Saved the plot as {total_name}")


###########################
# PyQTgraph Configuration #
###########################

#START QtApp 
# You MUST do this once to initialize pyqtgraph
# app = QtGui.QApplication([])  
app = QtWidgets.QApplication([])                                 

# Window title
WINDOW_TITLE = "Real Time Plotter"

# Set background white
pg.setConfigOption('background', 'k')
pg.setConfigOption('foreground', 'w')

# Define the window object for the plot
win = pg.GraphicsLayoutWidget(title=WINDOW_TITLE, show=False)

#Create button to save plots
# save_button = QtGui.QPushButton("Save Plot")
save_button = QtWidgets.QPushButton("Save Plot")

#Attach Callback 
save_button.clicked.connect(save_current_plot)


#Create the GUI
# window = QtGui.QWidget()
# hbox = QtGui.QVBoxLayout()
window = QtWidgets.QWidget()
hbox = QtWidgets.QVBoxLayout()  
hbox.addWidget(win)
hbox.addWidget(save_button)
window.setLayout(hbox)
window.show()

#Close view when exiting
app.aboutToQuit.connect(window.close)
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

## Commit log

2023-06-14 fixing file ordering
    [90592A080_Steel Hex Nut.STEP, 91125A039_Female Threaded Round Standoff.STEP, 91251A146_Black-Oxide Alloy Steel Socket Head Screw.STEP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]
2024-05-22 bill of materials
